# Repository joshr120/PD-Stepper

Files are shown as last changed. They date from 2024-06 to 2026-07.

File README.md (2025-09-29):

# **PD Stepper** - USB PD Closed Loop Stepper Driver & Controller
PD Stepper is a USB PD Powered Nema 17 stepper driver using the Silent Trinamic Driver TMC2209 controlled with a ESP32-S3 for IoT and other applications.

### Kits Available Now: [ThingsbyJosh.com](https://thingsbyjosh.com/products/pd-stepper) ###

<p float="left">
  
   
</p>

<p float="left">
   
  
</p>

Stepper motors are fantastic for projects, but assembling the necessary components—like a microcontroller, stepper driver, power supplies for both motor and microcontroller, and optionally an encoder can lead to bulkiness, high costs, complexity, and challenges in integrating them into compact or space-constrained designs. This project addresses these issues by consolidating everything onto a single board, eliminating the drawbacks with little to no compromises.

Full Video and build guide here: https://youtu.be/qECEGUZE04s?si=eJ1GiZOdusYehDCc

## Main Features: ##
- **TMC2209 Stepper Motor Driver:** Incorporates the TMC2209 stepper motor driver, renowned for its silent operation, high precision, and advanced features such as stealthChop™, spreadCycle™ and sensorless homing, ensuring smooth, silent and efficient motor control.
- **USB PD Power:** Utilizes the USB PD standard for power delivery, giving high power, a USB-C connector and no bulky 12 and 24V power bricks needed. It ensures compatibility with a variety of power sources and enabling seamless integration into existing setups. USB PD along with the TMC2209 can drive a stepper motor with upto ~50W of power.
- **Form Factor:** Super compact forma factor, designed to fit on the back of a common Nema 17 stepper motor
- **Onboard Rotary Position Sensor:** Integrates the AS5600 magnetic rotary position sensor for accurate and reliable absolute angle measurement, enabling precise positioning and closed loop control of the stepper motor.
- **ESP32-S3 Control:** The ESP32-S3 microcontroller serves as the brains of the system, providing ample processing power, built-in Wi-Fi and Bluetooth connectivity, and a rich ecosystem of development tools and libraries for easy customization and expansion such as **ESPHome** and **ESPNow**.
- Software or hardware selectable voltage: 5V, 9V, 12V, 15V or 20V all via USB PD
- Auxiliary connectors and buttons for flexablity and expansion
- Onboard 3.3V buck converter
- Motor temperature measurment

<p align="center">
  
</p>

## Kits Available For [Order](https://thingsbyjosh.com/products/pd-stepper) Now ##
   ### Subscribe on [YouTube](https://www.youtube.com/@ThingsbyJosh) for further updates. ###

<p align="center">
  
</p>

## Current Examples: ##
- Webserver allowing configuration, velocity and position control. (Comes pre-loaded on all kits, see [getting started](https://github.com/joshr120/PD-Stepper/tree/main/Getting%20Started) for how to use it.)
- Home automation with ESPHome and home assistant
- Wireless position copying from one encoder to another motor

## PCB: ##
PCB is a 4 layer 1.6mm custom PCB, this is what allows it to have its comapact form factor.
The Schematic, GERBERs and source files can be found in the PCB folder.

## Housing: ##
The Full Kits comes with an injection molded polycarbonate cover. This can also be 3D printed however PLA may not be suitable as the driver can get warm.

<p align="center">
  
</p>

## Cooling: ##
Stepper motor drivers can get warm under full load. The IC is cooled from the rear through a machined aluminium heatspreader which also acts as a spacer between the PCB and the motor. Two sizes of adhesive heatsinks can also stick to the top side with the larger one protruding through the housing and the smaller one siting just below the surface allowing the stepper to sit flat.

## Software: ##
The software is currently still evolving but current sample code should be more than enough to get you started

### ESPHome ###
The provided .yaml file allows you to control the motor through ESPHOME (setup as blinds in this example). It allows you to use the buttons as inputs and set the USB PD voltage. It also outputs the AS5600 encoder reading to be used within ESPHome. The USB PD voltage and stepper microsteps can be set at startup.

### Arduino Code ###
A few arduino examples are provided in this repo:
 - **Simple button control:**
   
      This example uses the buttons on the side to run the motor as at a variety of speeds as well as requesting a specified voltage from the PD controller. This can be used for a simple turntable and uses the simple step and direction interface to the driver

 - **Slider Webpage Control:**
   
      In this example the ESP32 hosts a webpage which allows you to wirelessly control the stepper motors speed with a slider. This utilises the [TMC2209 library](https://github.com/janelia-arduino/TMC2209) to configure the stepper driver.

- **ESP-NOW Sender and Receiver:**

     In this example one PD stepper board wirelessly sends its encoder value to another board which will mimic its position. This is an example of using ESP-NOW for low latency wireless communication.

  More info on the software can be found on the [software page](Software/README.md).

## Control ##
The primary way to control the PD Stepper is over WiFi (e.g ESPHome, ESP NOW or through a webserver) however there are many other ways you can control it

- Thanks to the pin mux on the ESP32-S3 the AUX connector (3 pin JST SH) can be used to send/receive commands over many different protocols. For example: Serial UART, I2C and standard STEP & DIR signals.
- By Using the I2C connector as well as the AUX connector you could daisy chain many PD Stepper boards together.
- The standard Qwiic / Stemma QT I2C connector (4 pin JST SH) means you can connect a wide range of sensors which could be used for control (for example a [Rotary Encoder](https://www.adafruit.com/product/5880) or a [Light Sensor](https://www.adafruit.com/product/4162))

- The 3 buttons on the side of the board can be set to control speed and/or position

- Serial commands can be sent/received through the USB-C connector (Note if your device sending the commands cannot provide enough power you may need an injector of some kind)

- The ESP32-S3 also has built in BLE (Bluetooth Low Energy) which could be used for control.

- End stops can also be connected to the AUX Connector (3 pin JST SH)

## Setting the driver voltage ##
The USB PD voltage can be set by toggling 3 GPIO pins on the ESP32. This can be configured on the fly to change voltage.

By default the board will ask for 20V at startup if the microcontroller does not set the config pins fast enough. If for whatever reason your motor cannot handle 20V you may want to set resistor R18 to a set value or ensure the pins are set on startup. The voltage can be configed by software on the fly as required. 

When programming the board it is likely your computer will only be able to provide 5V, the "Power Good" line from the PD controller can tell the ESP32 it is not receiving the voltage it is asking for and in this case you should proably not enable the stepper driver (as done in the example code)

NOTE: You must use a USB PD power brick/power bank which can provide the required voltage and current along with a suitable USB-C cable. QC (Quick Charge) is not currently supported.

## Setting the driver Current ##
The motor current can be set either in hardware with the onboard potentiometer or over the TMC2209 serial interface (see the [TMC2209 library](https://github.com/janelia-arduino/TMC2209) for more info on serial comms)

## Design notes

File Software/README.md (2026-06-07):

# **PD Stepper** - More Software Info

#### If you just received your PD Stepper see the [Setup Instructions](https://github.com/joshr120/PD-Stepper/tree/main/Getting%20Started) for how to get started

## Arduino Upload settings: ##
When uploading software with the Arduino IDE ensure you have first installed the ESP32 Add-on in Arduino IDE there are [many tutorials](https://randomnerdtutorials.com/installing-esp32-arduino-ide-2-0/) on how to do this.

The Board type should be set as "ESP32S3 Dev Module"

USB CDC on Boot should be set to "Enabled"

upload settings

## ESPHome: ##
>If you have not used ESPHome before follow the offical [getting started guide](https://esphome.io/guides/getting_started_hassio.html). Select ESP32-S3 as the board type. The custom .yaml can then be copied from the repo into the configuration editor. Ensure you also add you WiFi SSID and password to your "Secrets".

The **PD-Stepper-Blinds-Advanced.yaml** config file uses the [custom TMC2209](https://github.com/slimcdk/esphome-custom-components/tree/master/esphome/components/tmc2209) component by [slimcdk](https://github.com/slimcdk). It also uses the AS5600 encoder so that if the blinds are manually moved it will not lose its end positions. Thanks to the custom componenet the example cuses stall gaurd for sensorless homing. PD voltage and other settings can easily be configured in the settings section at the top of the code. 
> This will use the power on position as the OPEN position.

> If the motor spins but the cover stays in the "open" position it means either your encoder is not working or your motor is spinning in the opposite direction releative to your encoder. You can swap which lambda function is commented out to reverse the encoder direction. 

> Sensorless homing (Stallguard) is enabled whoch means if the motor stalls this becomes the new home (OPEN) position, you may need to tune the threshold and current values to get this to work well. See the settings section at the top to tune/disable.

The **PD-Stepper-Blinds-Simple.yaml** config file simply treats the TMC2209 as a a4988 driver. The microsteps and PD voltage are set at startup by GPIO pins and the motor is driven via the STEP and DIR pins.

The **PD-Stepper-Position-Control.yaml** config also uses the [custom TMC2209](https://github.com/slimcdk/esphome-custom-components/tree/master/esphome/components/tmc2209) component by @slimcdk. It is a more stripped down version of PD-Stepper-Blinds-Advanced.yaml allowing you to set the position of the motor using a simple slider. A good base for use cases other than blinds.

These examples also present the buttons, LEDs, power good and bus voltages to the ESPHome interface so you can do what you like with them.

## Flashing a precompiled binary online: ##

There is a great online tool called [ESPConnect](https://thelastoutpostworkshop.github.io/microcontroller_devkit/espconnect/) which can be used to flash the board without downloading any software. 

The following steps will show you how to flash the default webserver example.

**1.** Plug the PD Stepper into a PC, Open [ESPConnect](https://thelastoutpostworkshop.github.io/microcontroller_devkit/espconnect/) and press Connect.
image (3)

<br>
<br>

**2.** Select your board, COM number will be different but naming will be similar.
image (4)

<br>
<br>

**3.** Go to the "Flash Tools" page and select the `PD_Stepper_Web_Server.bin` file (Download from [here](https://github.com/joshr120/PD-Stepper/tree/main/Software/PD_Stepper_Web_Server)).
image (5)

<br>
<br>

**4.** Press flash and confirm
image (6)

<br>

Feel free to reach out at [info@thingsbyjosh.com](info@thingsbyjosh.com) if you have any problems.

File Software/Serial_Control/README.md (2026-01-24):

# PD Stepper: Serial Control Guide

Upload the Serial_Control.ino script to control your PD Stepper over serial.

## Connection Options

The controller supports dual-input serial communication. You can send commands through either interface; the controller will process the command and respond back on the same port it was received.

### 1. USB Connection (`Serial`)
* **Physical Port:** Standard USB-C connector on the ESP32-S3.
* **Baud Rate:** 115200

### 2. AUX Connector (`Serial1`)
* **Physical Port:** AUX connector (3 pin JST SH connector).
* **Pins:**
    * **Pin 1 (GND):** Ground pin.
    * **Pin 2 (AUX1 - TX):** Transmits data from the ESP32.
    * **Pin 3 (AUX2 - RX):** Receives data into the ESP32.
* **Baud Rate:** 115200

---

## Control Modes & Switching

The controller operates in a "last command wins" state machine. It switches between modes automatically based on the command received:

* **Position Mode:** Triggered by the `deg=` command. The motor will calculate the distance to the target angle and move using the speed defined by `speed=`.
* **Velocity Mode:** Triggered by the `vel=` command. This immediately overrides any active position targets and causes the motor to spin continuously at the requested rate.

> **Note:** Sending `vel=0` will stop the motor but keep it in Velocity Mode. To return to a specific angle, you must send a new `deg=` command.

---

## Encoder Integration (`MOVE_FROM_ENC`)

When `closed_loop_type` is set to `MOVE_FROM_ENC`, the controller uses the AS5600 Magnetic Encoder to verify its physical orientation before moving.

1.  **Read:** It captures the current mechanical angle from the encoder.
2.  **Calculate:** It determines the error (delta) between the current encoder position and your `deg=` setpoint.
3.  **Correct:** It generates the exact number of microsteps required to bridge that gap.

This allows the system to remain accurate even if the motor was moved by hand while the driver was disabled.

---

## Full Command List

| Command | Data Type | Description |
| :--- | :--- | :--- |
| `deg=` | Float | **Switch to Position Mode:** Move to absolute angle. |
| `deg_rel=` | Float | **Switch to Position Mode:** Relative move to absolute angle. (add or subtracts from current setpoint) |
| `speed=` | Float | Set travel speed for `deg=` movements (deg/s). |
| `vel=` | Float | **Switch to Velocity Mode:** Spin at fixed rate (deg/s). |
| `steps_per_rev=` | Int | Set motor physical steps (200 or 400). |
| `enable=` | Bool/Str | Enable/Disable driver (`1`/`0`, `TRUE`/`FALSE`, `enabled`/`disabled`). |
| `microsteps=` | Int | 1, 4, 8, 16, 32, 64, 128, or 256. |
| `voltage=` | Int | USB PD Request (5, 9, 12, 15, or 20). |
| `current=` | Int | Set run current as a percentage (0-100). |
| `standstill_mode=`| String | `NORMAL`, `FREEWHEELING`, `BRAKING`, or `STRONG_BRAKING`. |
| `closed_loop_type=`| String | `OPEN_LOOP` or `MOVE_FROM_ENC`. |
| `mappingDirection=`| Int | Reverse motor logic relative to encoder (`0` or `1`). |
| `verboseOutput=` | Int | Toggle confirmation messages (`0` or `1`). |
| `get_angle` | N/A | Returns current total encoder angle in degrees. |
| `values` | N/A | Lists all current configuration settings. |
| `led_flash` | N/A | Flashes LED1 twice for identification. |
| `help` | N/A | Displays summary of commands. |

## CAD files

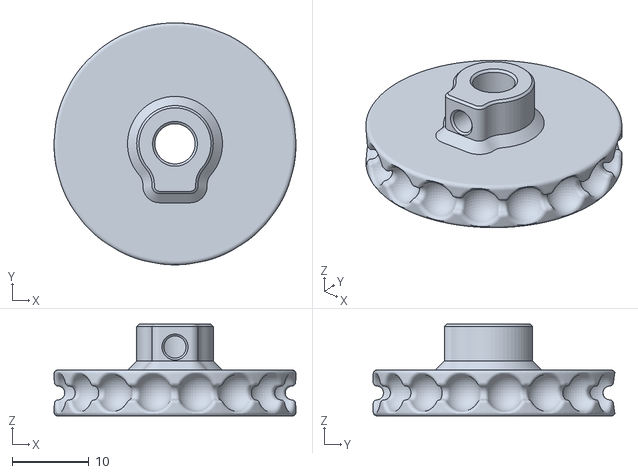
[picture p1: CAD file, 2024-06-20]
Hardware/Accessories/Blinds Wheel.stl
31.6 x 31.6 x 12.0

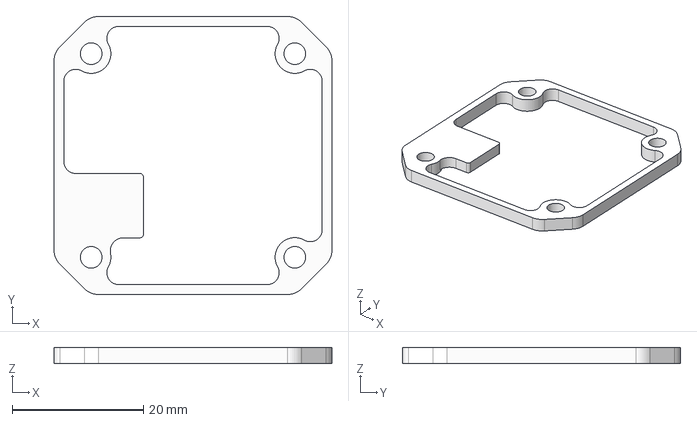
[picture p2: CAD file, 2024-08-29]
Hardware/Heat Spreader (2.5mm).step
42.3 x 42.3 x 2.50 mm

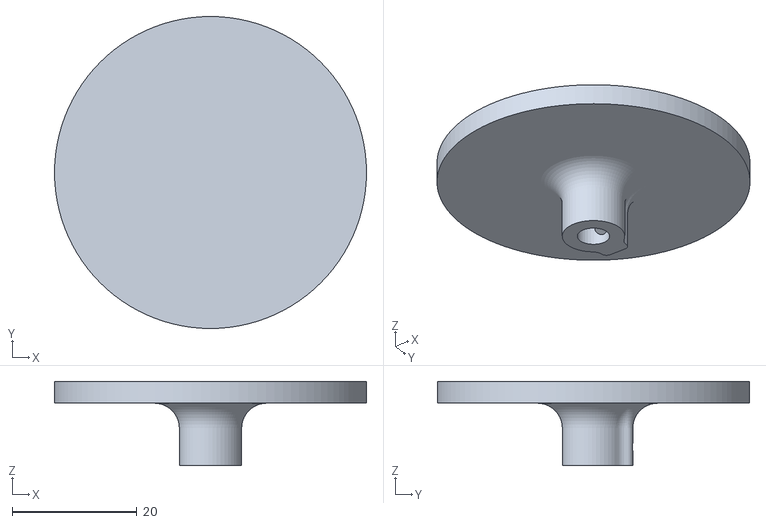
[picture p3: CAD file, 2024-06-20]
Hardware/Accessories/Turn Table.stl
50.0 x 50.0 x 13.5

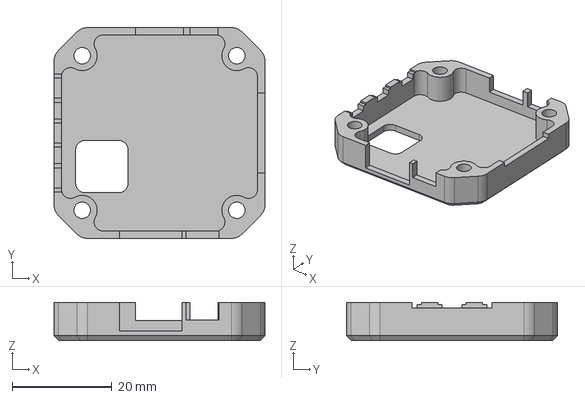
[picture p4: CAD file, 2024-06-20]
Hardware/Machined Housing.step
42.3 x 42.3 x 7.70 mm

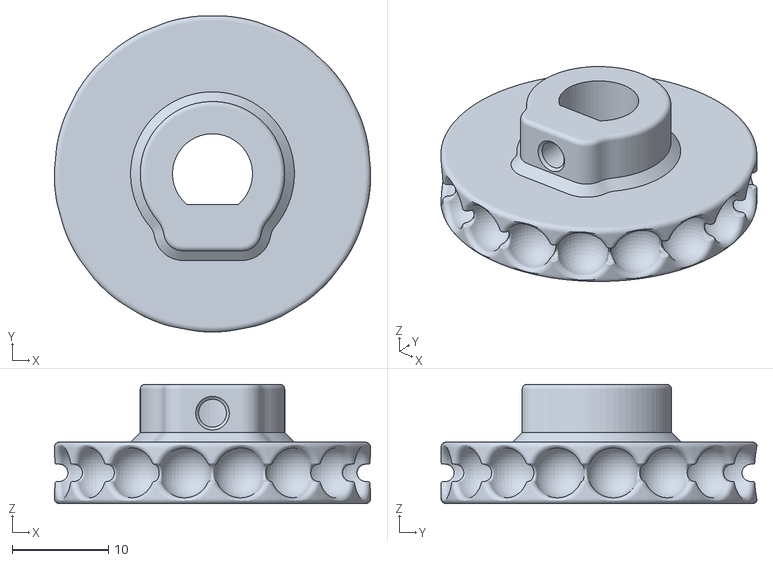
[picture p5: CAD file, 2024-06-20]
Hardware/Accessories/Wheel (8mm Bore).stl
32.8 x 32.8 x 12.4

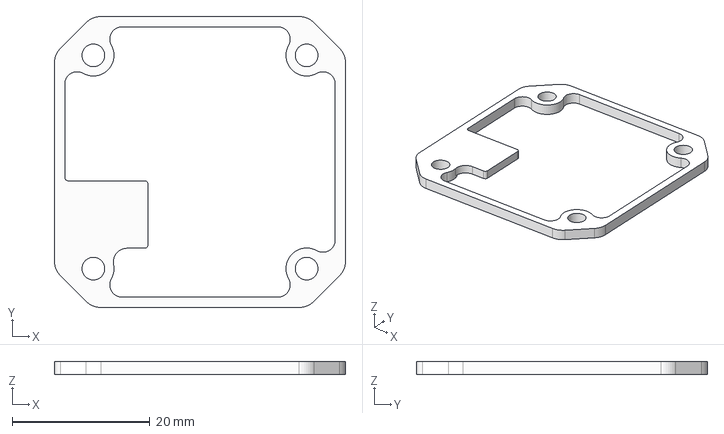
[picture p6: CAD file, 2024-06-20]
Hardware/Heat Spreader.step
42.3 x 42.3 x 1.95 mm

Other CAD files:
Hardware/Cover.stl

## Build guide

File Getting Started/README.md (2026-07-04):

# **PD Stepper** - Getting Started
If you just received your PD Stepper this will show you how to spin a motor and configure the driver using the firmware pre-installed on the board.

(Click [here](http://thingsbyjosh.com/canbus-stepper-getting-started) for the CANBUS Stepper getting started guide.)

⚠️ **Warning:** Stepper motors should never be back driven at a high speed as they can act as a generator and cause damage. This is especially important if your PD stepper board is connected directly to a computers USB port

## Assembling a kit onto a Nema 17 ##

Assembly is also shown in [this video](https://www.youtube.com/shorts/9y9dA18rnVY).

For easiest assembly your motor should have the stardard 6 pin JST PH connector, and the included screws (M3x40mm) are best suited for a 34mm length motor.
For example the Hanpose 17HS3401S, available on [Amazon](https://www.amazon.com/Captive-Stepper-17HS3401S-4-Lead-Printer/dp/B0G9KRJFTY) and [Aliexpress](https://www.aliexpress.com/item/1005006577156384.html).

### 1. Install the magnet onto your motor (only needed for reading encoder position)
   
   Carefully superglue the included diametrically magnitised magnet onto the centre of the motor shaft.  

   Only a very small amount of glue is required, take care not to get any in the motor bearing.  
   
   
   
### 2. Remove the original motor screws




### 3. Peel off the protective film and add one of the included heat pads onto the heat spreader

  Ensure this is added on the recessed side of the heat spreader
  



### 4. Place the spacer onto the motor ensuring it is in the orientation show

Note. If you are not using the heatspreader/spacer (partial kit) ensure the board is not resting directly on the motor as this could short out the traces on the underside of the PCB. Use washers or an insualting layer.



### 5. Add the PCB

Again ensure the PCB is installed in the orientation shown so the motor connectors as well as the heat pad line up




Note: Some motors may have longer shafts that make the magnet sit higher. If the sensor contacts the magnet, add spacers to raise the PCB.

### 5. Add the cover and new countersunk screws

   The included screws are best suited for a 34mm length Nema 17 you may need longer or shorter ones depending on your motor. (included ones are M3x40mm)
   
   
   

### 6. Add the heatsink

   Use the larger heatsink if you plan on running the motor for long periods and/or at high currents
   
   
   

### 7. Plug in motor loom

 There are 2 looms provided in the kit for different motors, try one and if at the next step your motor stutters/doesnt spin, power off the board and try the other one. 

  Note. Do not disconnect/connect the motor while the board is powered.

  

<br>
<br>

## Running the Webserver ##
**1.** Connect the PD Stepper to your PD power supply using a USB C to C cable (Needs to be Type C as USB PD does not support Type A).

**2.** Open a phone/computer and connect to the WiFi network named "PD Stepper"

**3.** Open a browser and type in the IP Address **192.168.4.1**


   
**5.** From here you can use velocity/postion control and play around with different settings.

**6.** The current is set as a percentage of the maximum possible current (1.92A). You will want to set this to match the current rating of your motor (or lower to stay cooler) E.g for a 1.8A motor set to 90% as 90% * 1.92A = 1.73A

Note: When using the webserver example the value is set here and the potentiometer is ignored. When using the advanced ESPHome examples this can be set with by changing the `run_current` value.

**7.** For your own projects this code as well as others (such as ESPHome config) can be found [HERE](/Software)

**8.** The buttons on the side can also be used to change the velocity

## Trouble Shooting ##
- The motor will not spin unless the board is receiving correct the voltage requested from the PD Source. So ensure your brick can supply the correct voltage and supports USB PD. The requested voltage can be adjusted on the fly in the webserver.
- If the "PG Status" is showing "Power Bad" ensure you are using a USB PD power supply (greater than 45W preffered) and that you are using a Type C to C cable.
- If the motor is not spinning smoothly, power off the board and try the other motor cable provided in the kit.
- If no WiFi network is created and LED 1 (blue) does not blink at startup, the correct software may not be installed. There are two ways to load the latest web server example software:

    The simplest method is to flash the precompiled binary using an online tool. See the instructions at the bottom of [this page](https://github.com/joshr120/PD-Stepper/tree/main/Software)

    Alternatively, you can compile and flash the Arduino source code located [here](https://github.com/joshr120/PD-Stepper/tree/main/Software/PD_Stepper_Web_Server)

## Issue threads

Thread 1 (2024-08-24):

Great idea, what are the memory limitations?

FlailAway, 2024-08-24:
The ESP32 appears to be limited to around 160KB. After setting up for local wifi, how does one handle data storage?

Streaming data-feed over wifi to a 3D-printer etc., would be a risky effort I would think, so a few GB of memory would be handy to store data in one complete block for it to feed forward.

Driving the blinds is a nice thing, but with closed-loop (terrific addition) greater things would need greater storage memory. No?

I don't do "G" or "YT" to comment there. :)

joshr120, 2024-08-24:
Instead of storing all of the movements on the devices you would feed them into a buffer (over USB or WiFi etc). Many people have used ESP32's to run CNC machines using this exact premise (See fluid NC for example). And the common GRBL software runs on an Arduino Uno which has significantly less memory, so I do not think this is an issue if you implement it correctly

Closed 2024-09-13.

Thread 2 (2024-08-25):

BOM - Bill Of Material

glennswest, 2024-08-25:
Great design.
BOM?

joshr120, 2024-09-18:
Send me an email at info@thingsbyjosh.com and I can get you a copy of the BOM

Closed 2024-09-18.

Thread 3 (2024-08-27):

GREAT IDEA! But more to add to it!!!!!

Cyrille-de-Brebisson, 2024-08-27:
Hello,

I LOVE YOUR IDEA. I just ordered one of the "standard" closed loop controler for a nema17, but yours is definitely one step above...

However, I have some requests/additional ideas here...

I am an amateur astronomer, and I make telescopes.
Telescope typically need 3 to 4 motors to work. 2 for moving the telescope, 1 for moving the focus and one for the filter wheel.
One issue that we have ALL THE TIME is cable managements. A typical astrophotography setup is a cable mess!

So, here is the request, Could the Aux connector be reworked so that it has:
- Data AND power
- They are 2 of them, one in, one out, in order to allow to daisy chain motors?

Thanks,
Cyrille

joshr120, 2024-08-27:
Hi Cyrille,

Thanks for the ideas, those particular connectors being used for AUX are only rated to 1 amp so would not have enough power to daisy chain multiple motors together. If you had multiple motors all running at full power powered off one USB PD port you could reach the max power draw pretty fast.
However, if you really wanted to daisy chain them there are solder pads on the underside where you can access/inject the PD voltage directly (just make sure you don't use the USB connector at the same time). Using I2C you could then daisy chain the data with the existing AUX and qwiic connectors . You could also use something like ESPNOW if you wanted to do this wirelessly.

Cyrille-de-Brebisson, 2024-08-27:
Hello,

I understand...

- Is it possible to have nice easy to solder vias for power daisy chain, with 2 of each (2 gnd, 2 power)? to make it easy and stable? something like a 2*2 1/10" header type thing?

- I see that you have a number of LED on the system. Some seems to be programmable (great), but others seems to be always on type thing. It is possible to have them controlable so that they can be turned off? As you can imagine, LEDs are not what you want near a telescope :-)

Cyrille

joshr120, 2024-09-18:
There is not currently room for extra power headers on the board at the moment, the solder pads on the underside are the best I could fit to stay within the NEMA17 form factor.

The additional LEDs are not currently set up to be able to be turned off in this version, although they are derated to not be full brightness. They can also be removed (or covered) if they are not needed.

fladdie, 2024-09-26:
Can bus would be a great feature

001oc, 2024-10-10:
Kicad: https://github.com/user-attachments/files/17332545/PD-Stepper.zip

EasyEDA: https://oshwlab.com/adamscamden2/pd-stepper

dwmw2, 2025-02-10:
What about expanding the motor connector to 6 pins to allow for power and ground through that?  I've just been playing with feeding power from behind, using S1761-R42 terminals. It works, but it's a real pain to solder up and assemble by hand, even in a mount 3D-printed for the purpose.

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

Using Veroboard is just as painful to solder but at least gives a better mechanical connection.

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

I'm tempted to get some tiny board professionally manufactured. Wonder if they'd be useful to include as an option in the kits? It could even be done as a full sized 42.3x42.3 board with the spring contacts on top and the PH connector on the bottom, designed to sit under the metal spacer/heatsink if the full kit?

joshr120, 2025-02-10:
Expanding the motor connector to 6 pins would mean that the motor loom could be plugged in the wrong way around (as the Nema 17 also has a 6 pin PH). This would also require the molds to be modified for the injection molded covers.

I do quite like the pogo pin idea.  The only problem I see with having the connector underneath like you do is it affecting the spacing between the magnet and encoder.  I guess you could add a spacer underneath the magnet or stack another magnet on top.
However a custom board could possibly replace the aluminum spacer and bring the connector out to the side and would not affect the form factor too much as you would already have wires coming out.

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

This mock up has it in front of the USB connector which would be a pain for programing but you really don't want both plugged in at the same time and this could fry your computer. This uses a 1mm board + a 1.6mm board to get the spacing as well as allowing a recess for the pogo's to sit in. Let me know what you think.

Could also be nice to use something which can carry a bit more current than a PH connector so that daisy chaining power could be an option.

dwmw2, 2025-02-10:
If I wanted it that side I'd just use the USB connector. I'm trying to keep the wires all on one side. This is the prototype version (inward facing, as I'm not allowed to dig holes in the wall until the proof of concept is working).

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

I'm trying to avoid that extra cable at the top. (Those green LEDs are too bright too but I'll try to hide those with a black cover).

I have my magnet mounted inside the gear, protruding through the piece of the mount that the power connectors are in, so that part works OK here. And I've found that soldering the spring connectors to a Dupont header designed for board-mounting seems to work...

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

joshr120, 2025-02-11:
Ah I see, did not realize your goal was to keep everything on one side. I thought you just wanted a way to power it with straight DC rather than USB PD.  Either way a custom PCB or 2 would probably be the way to go.

dwmw2, 2025-02-11:
The spacers require about 3mm between their base and the underside of the PD stepper board, so I think I'm happiest with my setup of soldering them to a Dupont header inset into the mount, rather than the thickness of an extra PCB.

But since someone else had already asked, I figured it was worth mentioning the possibility of a second PCB to supply power.

FWIW I also just realised I *do* need a plug at the top for the AUX pin which will be connected to the reed switch at the top of the blind, for homing. I'll probably bring that single wire straight down into the same plastic piece and bring it to a 3-pin header with the Gnd and Vbus I already have there. Are there unused GPIO pins on the ESP32? Maybe the QWIIC connector could have its *own* pins for its own i2c bus (or other purposes). The i2c bus with the as5600 encoder is going to be permanently busy with polling anyway, isn't it? Not much bandwidth for anything else.

joshr120, 2025-02-11:
Currently the QWIIC connector is on the same I2C bus as the as5600 as I was getting low on pins and that is how most of the QWIIC ecosystem works. If the encoder is being polled very fast it may use a fair bit of bandwidth but would also use a far bit of CPU bandwidth at the same time while reading, so a second bus may not be of too much use other than if there are address conflicts or you are getting fancy with multitasking.

I may look into putting it onto its own bus in a future version, but for something like a limit switch this is exactly why the AUX connector is there.

dwmw2, 2025-02-11:
The encoder needs to be polled fast, or it misses revolutions. I've been playing with it, and ESPHome going out to lunch seems to be the reason why my tracking was wrong. I occasionally see warnings like

```
[09:19:26][W][component:237]: Component as5600.sensor took a long time for an operation (4184 ms).
[09:19:26][W][component:238]: Components should block for at most 30 ms.
```
So the blind closes correctly because it did calculate the correct number of steps to turn the motor, but the encoder tracking only thinks it's closed part way. So when it's told to open again, it only goes part way.

But then #22 happened while I was experimenting and now I don't have a laptop so it'll be a little while before I can experiment some more...

joshr120, 2025-02-11:
yes you need to be reading fast enough to catch a wrap around. Just did some quick timing with Arduino and a read takes ~500 microseconds so you would need to be polling around 2000Hz to max out the bus.  The max speed of a stepper is _relatively_ slow so you should never run into the problem of not being able to poll fast enough to catch a wrap around.
It does sound like your problem is ESPHome related. It may actually be polling too fast and hogging the CPU which ESPHome may not like, you could try slowing down the polling rate.

dwmw2, 2025-02-11:
I think I'd already backed the poll rate down to 50ms from the originally configured zero, after seeing ESPHome watchdog resets because the idle task was never getting to run. That should have been fine.

Closed 2025-05-28.

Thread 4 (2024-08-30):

KICAD files available

001oc, 2024-08-30:
great idea you realized, matching a project I was looking a solution for some time now. I would like to expand the projekt abit for my needs are KICAD files (or something else) available?

Thanks

Johnr24, 2024-09-10:
Yes, +1 Please supply the kicad or original source files. You can't truly call your project open-source if you aren't providing the easiest and least resistive way of allowing users to make changes and alterations...

joshr120, 2024-09-18:
The PCB Source files are not available at this stage sorry, feel free to use the schematic and GERBERs to base your project on.

Johnr24, 2024-09-18:
this is not compliant with GPL see section 7. Gerbers and Schematics are effectively compiled binaries and not source files,

001oc, 2024-09-18:
I think it would and should be his decision the way he feels it would be open source or something similar ... and we have to accept it instead of poking arround. I think it is well made and I dont blame someone to try to make some money to get back its efforts making some valuable pcb. And its way not to complicate to rebuild it - what I am doing right now. I am doing currently a rough "rebuild" of the pcb. Its purpose should be to help that people which want do expand or modify the good base idea - as me. I think that this is not disturbing the business of @Johnr24 as the onces that want to modify the pcb even are no potential customer of @Johnr24 - I think that could be a point of view even for @Johnr24 - but as I sayed, not my decision.

I am happy for the material that is already posted and it helps me to redesign the pcb quit quickly I think - from my point of view this is more than enough and I am thankful for that.

SoupySoups, 2024-10-10:
I know im gonna get some backlash for easy eda but i have recreated the board with my own differences [here ](https://oshwlab.com/adamscamden2/pd-stepper). Everything works great from my tests.

001oc, 2024-10-10:
Thanks alot to @SoupySoups .

I have imported your stuff to Kicad roughly.

From my quick overview it seems to be working - at least it is a proper base to work further.

[PD-Stepper.zip](https://github.com/user-attachments/files/17332545/PD-Stepper.zip)

Johnr24, 2024-10-10:
Excellent. Amazing work!  Could I suggest starting a fork of this project
that is truly and correctly open source?

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

tmarkson, 2024-10-10:
The fact that you could redraw Josh's design from the files that he provided suggests the project is open enough already!

joshr120, 2024-10-11:
Now that pre-orders are starting to be shipped I have published the PCB Files (Altium format).
I also had a quick look at @SoupySoups easyeda project and can offer a few pointers which will help it work better if someone plans on using those files.

Main reason I did not release them earlier was to stop someone simply slapping their logo on it and beating me to market while I was ramping up production & waiting for molds to be made. (Full kits will now come with injection molded polycarbonate covers and a black anodized heat spreader/spacer).

SoupySoups, 2024-10-11:
> Now that pre-orders are starting to be shipped I have published the PCB Files (Altium format). I also had a quick look at @SoupySoups easyeda project and can offer a few pointers which will help it work better if someone plans on using those files.
>
> Main reason I did not release them earlier was to stop someone simply slapping their logo on it and beating me to market while I was ramping up production & waiting for molds to be made. (Full kits will now come with injection molded polycarbonate covers and a black anodized heat spreader/spacer).

I understand your reasoning, I recreated the design not to sell the product but to put in a project i am currently designing in which i needed multiple of these steppers. I understand the extra value that you provide other than the raw pcb but i did not need the extra parts and the cost for 8x kits per unit of my design just did not make economic sense for my application.

The copy in easyEDA was rushed and im not that great at PCB design but all functionalities (i removed some of your features that I didn't need to further save costs and make layout easier, aka. buttons and expansion). Everything seems to work well though.

In all, yeah, your board is reeeeeally nice. I wish i had your skills, and I agree, mine is not meant to be sold in a kit, its rough.

> The fact that you could redraw Josh's design from the files that he provided suggests the project is open enough already!

In response to this, its tough, wouldn't call having to go through grbl files manually "open".

Josh I appreciate this and am thankful for what was shared, even if difficult. I notice you dont have any example code with measuring vbus voltage, using the temperature sensor, or using the AS5600 in combination with the TMC2209 for closed loop stepper control. If you would like, I would be more than happy to share my code, implementing such features.

Closed 2024-09-18.

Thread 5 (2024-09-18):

not compliant with GPL

Johnr24, 2024-09-18:
as the source kicad files have not been provided,
this is not compliant with GPL see section 7. Gerbers and Schematics are effectively compiled binaries and not source files,

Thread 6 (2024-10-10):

Kicad and EasyEDA files available now...

001oc, 2024-10-10:
For further development there are files for Kicad and EasyEDA available:

Kicad: https://github.com/user-attachments/files/17332545/PD-Stepper.zip

EasyEDA: https://oshwlab.com/adamscamden2/pd-stepper

Cyrille-de-Brebisson, 2024-10-11:
Hello,

One request, if possible. Would it be possible to add 2, 2 pins headers with GND and vbus?

The aim would be to be able to bring power to stepper "one" (either using USB or a 12V power supply), and then daisy chain 3 or 4 steppers from there. I do not have a huge power consumption (around 1A for the 2 main motors, who are only running for short intervals), and around 0.5A for the 2 others which will run around 1 minute per night each...

I tried looking at the PCB to see if I could do it myself, but I am way not good enough to start playing with such a non-trivial PCB (is it a 4 layers PCB?)

Thanks,
Cyrille

001oc, 2024-10-11:
> Would it be possible to add 2, 2 pins headers with GND and vbus?
I think there seams to be enough free space to do so. Anyway, I wouldn't do that this way,

>  (is it a 4 layers PCB?)
no, its a "simple" 2-layer pcb

Cyrille-de-Brebisson, 2024-10-11:
Hello,

>>   Would it be possible to add 2, 2 pins headers with GND and vbus?
>I think there seams to be enough free space to do so. Anyway, I wouldn't do that this way,
How would you do it?

I am trying to use these motors to make a telescope mount...
Telescopes have WAY to many cables! this should give you an idea of the mess that you can get into :-) https://i.ytimg.com/vi/Ip0Ok9OncNY/maxresdefault.jpg

Anyhow, on the other hand, we DO have 12V available to us as all astro equipement uses "raw" 12V...
Typically, we use a slow discharge car battery with a 12V boost converter to generate said 12V...

However, finding a USB-C power supply (portable) that will have 4 PD output and will run on 12V would be quite hard...
Plus it will cause tnagled wires as the scope moves..

Hence the idea of being able to connect the motor in a daisy chain (or distribution tree as needed) in order to reduce cables and cable snags.

Cyrille

joshr120, 2024-10-11:
Now that pre-orders are starting to be shipped The Altium Source Files been added to the repo.

Closed 2024-10-11.

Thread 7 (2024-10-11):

proposed Altium sources and existing Kicad and EasyEDA sources

001oc, 2024-10-11:
Now that pre-orders are starting to be shipped The Altium Source Files been added to the repo.

_Originally posted by @joshr120 in https://github.com/joshr120/PD-Stepper/issues/6#issuecomment-2406915418_

I can't see the altium files as of now and there is even no specific hint where to look specifically. Even most people will not have a Altium license. For that reason I will repost the Kicad and easyEDA sources to get people an easy way to work further on this project.

As @joshr120 stated the reason for not revealing the sources till now is not to be beaten in getting his project to market. That should be no problem now. For that reason it  shouldn't be neccessary to close the issue that fast because that will prevent others to get the information where to get sources - otherwise one could have the impression @joshr120 intention is to supress such information for an gpl-project.

Please let this issue open for now.

Kicad: https://github.com/user-attachments/files/17332545/PD-Stepper.zip

EasyEDA: https://oshwlab.com/adamscamden2/pd-stepper

joshr120, 2024-10-11:
I committed the files but forgot to press push 🤦 my bad. The files can be found in the PCB folder. They are in Altium format as that is what the board was designed in. These can however be [converted to your PCB design software of choice.](https://refcircuit.com/articles/18-how-to-import-altium-designer-pcb-board-in-kicad.html) From my quick look at the easyeda design by @SoupySoups there were a couple of potential issue I spotted as well as not all features supported so I would recommend any future modifications are based off the fully tested files now that they are available.

I closed the previous issue as the original fully tested PCB files are now available so I considered it solved. Can keep this issue open for a while if you would like? The closed issues are still available for anyone to see.

001oc, 2024-10-11:
Thanks alot :-)

SoupySoups, 2024-10-11:
> I committed the files but forgot to press push 🤦 my bad. The files can be found in the PCB folder. They are in Altium format as that is what the board was designed in. These can however be [converted to your PCB design software of choice.](https://refcircuit.com/articles/18-how-to-import-altium-designer-pcb-board-in-kicad.html) From my quick look at the easyeda design by @SoupySoups there were a couple of potential issue I spotted as well as not all features supported so I would recommend any future modifications are based off the fully tested files now that they are available.
>
> I closed the previous issue as the original fully tested PCB files are now available so I considered it solved. Can keep this issue open for a while if you would like? The closed issues are still available for anyone to see.

Would you be willing to share such issues? From initial testing, all features that I chose to implement seem to be functioning correctly.

joshr120, 2024-10-12:
Sure, I have not looked too in depth but here are couple of things I noticed that may affect performance. Other than the features you intentionally did not include the first thing I noticed was the setup of the current sensing resistors for the TMC2209. These carry the full motor current and currently your design does not have well defined return path from the resistors back to the IC. The GND pad on the TMC is not accessible on the top layer and the layers are only really stitched with the vias in the corner mounting holes. Adding a few GND vias near the GND pads of these resistors would help greatly.

Here is a screenshot from the TMC2209 datasheet which explains why it needs to be carefully considered:
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

I would also probably want to increase the trace width between the current sense resistors and the TMC as these take the full motor current.

Decoupling caps for the various IC's as well as the VIN and VOUT caps for the 3.3V reg should be placed as close to the relevant pins as possible.

Hope these tips help with your future designs!

SoupySoups, 2024-10-12:
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

Oh yeah, that gnd section isnt very connected 😅

Closed 2024-10-11.

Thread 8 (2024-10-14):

Not a problem, but a question

Cyrille-de-Brebisson, 2024-10-14:
Hello,

I have noticed with the traditional drivers that microsteps are NOT all equal.

For example at 1/8th using an A4988, the various microsteps are definitely not 0.225° appart (360/200*8). Although 8 microsteps do indeed equal 1.8°
DRV8825 at 1/32 are much better, but even then, microsteps are not concistent...
(These are tests that I did using a mirror on a motor and measuring the displacement of a laser 5m away)...

So, here is the question. In your design you have a TMC2209 with 256th microsteps, but also the 14 bit position sensor (which give the equivalent of a 1/80th microstep precision, and is, itself not truly linear according to the datasheet)...
Would it be possible to generate a 51200 entry table that gives, for each of 200*256 microstep, the sensor reading in order to characterize the real position for each microstep?

Thanks,
Cyrille

joshr120, 2024-10-15:
Hi Cyrille,

The "microstepping consistency" of the TMC2209 should be a lot more accurate than the A4988.

To answer your question I imagine the characterization you are looking for would likely change depending on a number of factors such as static friction of the motor, winding quality, how centered the magnet is on the encoder, etc. The linearity of the AS5600 will also depend quite a lot on how centered the magnet is on the sensor (Although this would stay consistent for each setup so could be calibrated out)

However, I have done a quick test as you asked and made a table showing encoder reading vs microsteps. (400*256 = 102400 data points as my motor was a 400 step per revolution stepper). Note this test was just run at 5V with not a whole lot of effort put into exactly centering/spacing the magnet.

Data can be found here: https://docs.google.com/spreadsheets/d/1EG3RP1kZXmzleNbZcZI58o96MoQLjMxshMYBuX7mUSY/edit?usp=sharing

This data also does not answer the first part of your comment as the encoder is 14 bit (0.088 deg accuracy) and each microstep in this case is only 0.0035 degrees

Thanks,
Josh

Cyrille-de-Brebisson, 2024-10-15:
Woha, thanks!

I will be looking at the data and commenting back here, but thank you so much for doing the work!

Cyrille

joshr120, 2024-10-16:
The difference between your "Series 1" and "Series 2" was just because of my hastily written test code which had a routing error accumulating for each step taken. The "Series 2" in your graph is the correct error measurement. I have fixed the code for these next tests.

The longer oscillation is the most likely due to the sensor not being aligned with the magnet very well. Because this stays consistent for each setup (and returns to 0 after each rotation) it can be easily calibrated out by running the motor with no load and recording the expected position vs encoder reading.

I have re-run the test with a simple calibration for comparison. The calibration was very simple and just a lookup table of encoder reading vs "actual" position.

The data has been added to a new tab in the [spreadsheet](https://docs.google.com/spreadsheets/d/1EG3RP1kZXmzleNbZcZI58o96MoQLjMxshMYBuX7mUSY/edit?usp=sharing).

And here is the a graph showing error with and without calibration.
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

I am not aware of any higher resolution drop in replacements for the AS5600 as most higher resolution encoders use a SPI or alternative interface to also get additional bandwidth.

Cyrille-de-Brebisson, 2024-10-16:
Hello,

1.2° of error seems A LOT!

But who cares, once it is calibrated, it indeed drops to what amounts to 0! Great job...

Thanks for taking the measurements..
Cyrille

Closed 2025-05-28.

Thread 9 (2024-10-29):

Beautiful cover! Where did you get injection molded polycarbonate cover

wasauce, 2024-10-29:
@joshr120 - wonderful project here and really compelling.

I am working on a cover for a totally different project (no stepper motor) and I am inspired by your injection molded polycarbonate cover. Could you share more about where you get these covers made? I am new to this and looking to learn.

I don't have a good sense of the cost as compared to some 3d printed solutions and I'd love a pointer in the right direction.

Thank you!

Closed 2024-11-17.

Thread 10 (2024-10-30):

Ethernet question

under-score, 2024-10-30:
great device. Can I attach an ethernet/USB C adapter and use  incoming PTZ commands for motor movements?

joshr120, 2024-10-30:
It may be technically possible but probably not very feasible. The ESP32 would need to act as USB host and you would need to write drivers for the specific USB-Ethernet chip.
You would also need some sort of UDB PD power injector to power the stepper driver at the same time.

Closed 2024-10-31.

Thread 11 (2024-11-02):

Suggestion to add caution for installation when not using heat spreader

jgueydan, 2024-11-02:
It might seem obvious to most, but you may want to add a caution in your Read Me description that if someone purchases the standard kit (without heat spreader) that they SHOULD use either spacers or other insulated material between the PD Stepper and the motor body to keep from shorting out the board.  Can't say enough about how much I love this board and it's endless possibilities for use!!  Very well done Josh!!  I'm not a programmer at all, so the included default firmware is great for testing and I very much appreciate it, plus the examples you provided in the software section.

joshr120, 2024-11-04:
I am in the process of creating some more in depth assembly instructions so will be sure to include a note about it. Thanks for pointing it out.

Closed 2024-11-17.

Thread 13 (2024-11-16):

Can you make a new Yaml using this custom component please

wshankles, 2024-11-16:
https://github.com/slimcdk/esphome-custom-components/tree/master/esphome/components/tmc2209

joshr120, 2024-11-17:
This is being worked on should be released shortly

joshr120, 2024-11-17:
New .yaml files have been added to the [ESPHome folder](https://github.com/joshr120/PD-Stepper/tree/main/Software/ESPHome) using the custom [TMC2209 component](https://github.com/slimcdk/esphome-custom-components/tree/master/esphome/components/tmc2209) thanks to @slimcdk

Let me know how you get on

Closed 2024-12-05.

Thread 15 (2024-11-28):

arduino fails to compile

amauryverschooren, 2024-11-28:
https://github.com/joshr120/PD-Stepper/blob/614ef368d68fe608b0ca06e0aee6fc43efc8a80e/Software/PD_Stepper_Web_Server/PD_Stepper_Web_Server.ino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

https://github.com/joshr120/PD-Stepper/blob/614ef368d68fe608b0ca06e0aee6fc43efc8a80e/Software/PD_Stepper_Web_Server/PD_Stepper_Web_Server.ino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

these 2 lines should have const before them.

joshr120, 2024-11-30:
Have you modified the code at all? Seems to compile fine for me in both Arduino IDE 1 and 2

joshr120, 2025-01-09:
I have done some testing and found it likely comes from using the wrong ESPAsyncWebServer library.

I replicated the error when using a fork of the original library: [https://github.com/mathieucarbou/ESPAsyncWebServer](https://github.com/mathieucarbou/ESPAsyncWebServer)
Compiles fine using the original library: [https://github.com/me-no-dev/ESPAsyncWebServer](https://github.com/me-no-dev/ESPAsyncWebServer)

I suggest either change libraries or add const to lines 281 and 292 as @amauryverschooren suggested

Let me know how you get on

amauryverschooren, 2025-01-09:
Hi Josh

Switching to the other library fixed it for me!

Thanks for the help!

Closed 2025-01-09.

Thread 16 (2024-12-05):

What is the AUX connector?

pvince, 2024-12-05:
What type of connector is the AUX connector?

I was looking at adding a contact sensor and wanted to know what kind of crimper // connectors I will need to buy.

joshr120, 2024-12-05:
The AUX connector is a 3 pin JST SH connector. Genuine crimpers can be quite expensive but plenty of places also sell pre-crimped leads: https://www.adafruit.com/product/5765

pvince, 2024-12-05:
Thanks! Could you update the documentation somewhere with that information? (That it is a 3 pin JST SH connector)

joshr120, 2024-12-07:
Will do!

Closed 2024-12-07.

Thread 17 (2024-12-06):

YouTube link is broken

poptix, 2024-12-06:
Your YouTube link in the README.md links to https://www.youtube.com/@ThingsbyJosh-bg9cv which 404's, should be https://www.youtube.com/@ThingsbyJosh

Thanks for the awesome products, mine arrived today!

joshr120, 2024-12-07:
Thanks for pointing that out all fixed now. Hope you find a good use for the board!

Closed 2024-12-07.

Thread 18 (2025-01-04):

[Question] Can I power the module with 12V dc?

schmelly, 2025-01-04:
Dear Josh,

maybe a slightly dumb question but I can I power the module with a 12V dc supply instead of a usb-pd supply?

Background: I intend to use the module to drive a stepper motor for autofocusing an astrophotography setup. Here, typical supply voltages are 12V dc and an approriate connector would be available already in my setup.
If a dc supply won't work this wouldn't be a problem either. I just would have to route an additional usb-c cable to my telescope which would be just a bit more inconvenient.

Thanks and best regards, David

joshr120, 2025-01-04:
Hi David,

There are solder pads on the underside of the PCB where you can directly connect a DC supply of upto 20V.
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

Just make sure you do do not have both the USB and DC power connected at the same time.

Thanks,
Josh

schmelly, 2025-01-05:
Thanks for your prompt support Josh! :-)

Best regards, David

Closed 2025-01-05.

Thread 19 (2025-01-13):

Please document motor current limits

dwmw2, 2025-01-13:
Thanks for this project; it's great. I've just received three of them.

I'm trying to understand the current settings, so I can hook them up to my (2.4V 1.5A 1.6Ω) stepper motors. I was hoping to find something about that in the QuickStart documentation.

Trying to work it out for myself... you have external 100mΩ resistors on BRA/BRB for Rsense. So according to the table in §8 of the TMC2209 datasheet, that gives a max RMS current of 1.92A, when the VREF input is >=2.5V and IRUN is 31.

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

I think the 'current percentage' in the web interface corresponds to IRUN, with 100% mapping to the value 31.

And it looks like the R10 potentiometer allows me to scale VREF from about zero to 2.5V, and you ship it set in the middle, which should mean 100% is 0.96A?
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

So for a 1.5A motor I can either set R10 to its maximum _(or clear GCONF.i_scale_analog which has the same effect?)_ and configure the PD Stepper for 78% (25/32), or actually try to precisely set R10 to give me a VREF of 1.95V?

Without putting probes on the board there's no way to actually read what I've set R10/VREF to, is there?

dwmw2, 2025-01-13:
Hm, doesn't clearing GCONF.i_scale_analog mean VREF is ignored... and doesn't the TMC2209 component do exactly that? https://github.com/slimcdk/esphome-custom-components/blob/master/esphome/components/tmc2209/tmc2209_component.cpp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

Does that mean VREF from R10 is ignored in the software that's shipped by default?

slimcdk, 2025-01-13:
> clearing GCONF.i_scale_analog mean VREF is ignored...

Correct. VREF is ignored with `I_scale_analog = 0` and current scaling is controlled through `IRUN` and `IHOLD` registers via the [`tmc2209.currents`](https://github.com/slimcdk/esphome-custom-components/tree/master/esphome/components/tmc2209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) action. `I_scale_analog=1` will use VREF and ignore values in said registers. You can overrule that initial setting by [writing to the register](https://github.com/slimcdk/esphome-custom-components/tree/master/esphome/components/tmc2209#advanced) from an `on_boot` action, if you wish to experiment.

Having the input on VREF for a hardware project like this adds more flexibility for the end user. Anyway, feel free to open a ticket on my project for further discussion on adding in this configuration option.

dwmw2, 2025-01-13:
> `I_scale_analog=1` will use VREF and ignore values in said registers.

Hm, is that true? I thought `IRUN` and `IHOLD` were still applicable whether `I_scale_analog` is set or not.
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

> You can overrule that initial setting by [writing to the register](https://github.com/slimcdk/esphome-custom-components/tree/master/esphome/components/tmc2209#advanced) from an on_boot action, if you wish to experiment.

Your docs tell me that doing that may cause instability in the ESPHome component and should be avoided :)
It also looks like you have a `CONF_ANALOG_SCALE` defined in the config already; I'm just not sure it's wired up.

In fact I don't think I *want* to use VREF, as I have no simple way of measuring what I've set it to. For now I'm just trying to understand how to set the thing up. I *think* that it's configured to ignore VREF by default, so I should just set the current percentage to 70% and that should do the right thing.

dwmw2, 2025-01-13:
Ah, the software on the device as it's shipped isn't ESPHome; it's [this](https://github.com/joshr120/PD-Stepper/tree/main/Software/PD_Stepper_Web_Server) one which uses https://github.com/janelia-arduino/TMC2209. So maybe VREF *is* applicable to the device as it's shipped? So I should probably turn it to max and then set IRUN to 70% (and check it doesn't catch fire).

joshr120, 2025-01-15:
My understanding it that in both the default webserver case as well as when using ESPHome with the component by @slimcdk I_scale_analog is set to 0 and the VREF is ignored.

I have verified for both cases by adjusting the potentiometer to it's extremes and feeling no difference in the force required to stall the motor.

I will update the getting started guide with a bit more info on how to select the current. I may also update the webserver to give values in the drop down instead of a percentage.

As a side note if you do want to measure VREF there is a test point on the underside of the board.

dwmw2, 2025-01-15:
Thanks! The dropdowns in the webserver probably shouldn't be in multiples of 10% either, should they? Each step in `IRUN` is actually about 0.06A, so the options are:

 - 3% / 60mA
 - 6% / 120mA
 - 9% / 180mA
 - 12% / 240mA
 - 15% / 300mA
 - 18% / 360mA
 - 21% / 420mA
 - 25% / 480mA
 - 28% / 540mA
 - 31% / 600mA
 - 34% / 660mA
 - 37% / 720mA
 - 40% / 780mA
 - 43% / 840mA
 - 46% / 900mA
 - 50% / 960mA
 - 53% / 1.02A
 - 56% / 1.08A
 - 59% / 1.14A
 - 62% / 1.20A
 - 65% / 1.26A
 - 68% / 1.32A
 - 71% / 1.38A
 - 75% / 1.44A
 - 78% / 1.50A
 - 81% / 1.56A
 - 84% / 1.62A
 - 87% / 1.68A
 - 90% / 1.74A
 - 93% / 1.80A
 - 96% / 1.86A
 - 100% / 1.92A

That's not taking a 10% safety margin into account, and it's assuming all current values are in RMS not peak. For my 1.5A motor (which I'm assuming is 1.5A RMS) I'll choose the 71% option, `IRUN=0x16`.

dwmw2, 2025-01-15:
> As a side note if you do want to measure VREF there is a test point on the underside of the board.

Could that be run to an ADC input pin on the ESP32? Or would that cause too much noise?

joshr120, 2025-01-16:
It probably could be fed into an ADC but as it is disabled for most use cases probably not worth it

slimcdk, 2025-02-13:
I spend a bit of time investigating this further (while also adding the option [`analog_current_scale`](https://github.com/slimcdk/esphome-custom-components/blob/master/esphome/components/tmc2209/README.md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) to set `I_scale_analog` for the ESPHome component) and has now concluded the following.

* `I_scale_analog=0`  ignores any input from VREF and solely scale currents from what is set in IRUN register.
* `I_scale_analog=1` appear to take both VREF _and_ IRUN into account such that VREF scales from 0 to what is in the register. So, VREF at 2.5V is equal to what is set in the register.

Have you tested this and could perhaps confirm my experience? This is not the behavior I understand from reading the docs.

dwmw2, 2025-02-13:
I think that *was* the behaviour I understand from reading the docs, as cited in https://github.com/joshr120/PD-Stepper/issues/19#issuecomment-2587626229 above?

slimcdk, 2025-02-13:
Maybe I read it wrong, but I interpret the docs (and your comment) as "VREF determines the scaling of IRUN" rather than "VREF scales _up to_ IRUN", if that makes any sense. I would argue there is a key distinction here: in the latter case, VREF alone couldn't set full current unless IRUN is at its maximum (31). In contrast, if VREF directly scales the current, it could do so regardless of IRUN's value. That’s why I originally argued that `I_scale_analog` configured either VREF or IRUN scaling determines the current, but what I've later experienced isn't the case. Perhaps you can find time to replicate what I've experienced?

Anyway, I don't think VREF should be used, unless there is a setup where the hardware was specifically designed for it, which isn't the case in this project.

slimcdk, 2025-02-13:
Yep, in either case IRUN will always scale the current. If `I_scale_analog=1`, then VREF adds onto that.

Closed 2025-03-27.

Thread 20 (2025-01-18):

Help With Stemma

Phando, 2025-01-18:
Is there an example of using a rotary via the stemma connector?
Do I need to set up the stemma pins in my platformio project? If so, what pins are used in the stemma connector.
Is there a platformio board definition for the Esp32-S3-PDStepper?

Thank you!

joshr120, 2025-01-18:
For rotary encoder examples this will very much depend on what module/device you are connecting to it so there are not any examples as part of this project. You will want to refer to the module you are using as to how to use it.

The STEMMA QT connector uses I2C and the pins are as follows:
```
#define SCL     9
#define SDA     8
```

This is already setup in most of the examples as it is on the same bus as the built in AS5600 encoder.

There is not a custom board definition for the PD Stepper but you should just be able to use a generic ESP32-S3 dev board if you would like.

Phando, 2025-01-18:
Thanks for the quick reply! I  using the adafruit led rotary encoder. I’ll check more examples.On Jan 18, 2025, at 2:16 PM, joshr120 ***@***.***> wrote:
For rotary encoder examples this will very much depend on what module/device you are connecting to it so there are not any examples as part of this project. You will want to refer to the module you are using as to how to use it.
The STEMMA QT connector uses I2C and the pins are as follows:
#define SCL     9
#define SDA     8

This is already setup in most of the examples as it is on the same bus as the built in AS5600 encoder.
There is not a custom board definition for the PD Stepper but you should just be able to use a generic ESP32-S3 dev board if you would like.

—Reply to this email directly, view it on GitHub, or unsubscribe.You are receiving this because you authored the thread.Message ID: ***@***.***>

Closed 2025-02-11.

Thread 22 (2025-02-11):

Reverse voltage protection

dwmw2, 2025-02-11:
With the stepper PCB unpowered, if I pull the blind cord manually the motor appears to provide power and the green LED lights up.

With the stepper PCB  powered but idle (in freewheeling mode), the board seems to crash if I pull the blind cord manually above a certain speed.

With the stepper PCB powered from my laptop... my laptop now appears to be completely dead and won't power up at all any more

joshr120, 2025-02-11:
Stepper motors generate back EMF when being back driven and act as a generator. This is very common and devices with stepper motors such as 3D printers should never be back driven too fast. The PD stepper is no exception to this.

Some servo motors will have a braking resistor to soak up some of this generated energy. A large TVS diode on the power rail can also help with shorter spikes but will only be so effective for a continuous reverse power generation.

If the back EMF is over 22V then the buck converter may not longer be able to effectively regulate the 3V3 rail. This is likely what is causing the board to crash in your second scenario once the motor reaches a certain speed.

I will add more warning notes throughout the documentation not to back drive the motor quickly. This is especially the case when a computer is connected, in general a motor should not be spun when powered from a computer (The Arduino sketches all disable the stepper driver unless powered via PD to avoid drawing too much current from a computer).

If you have blown up a motor board let me know and I can send out a new one.

dwmw2, 2025-02-11:
Is it possible to gate the connections from the motor to the TMC2209 with MOSFETs, so they're only connected when it's actually trying to *drive* the motor?

I think the board is OK, but anyway you've already sent me a spare motor board, thanks! I just ordered a fourth so I have a spare, after noticing that one of my first three has one of the buttons missing (probably from my repeated assembly/disassembly of 3D mount parts).

I'm more worried about the laptop at this point. :)

Arguably *it* should have better protection on its USB port too.

Could the PD stepper board at least have a diode to prevent killing whatever is on the USB port? If the stepper PCB itself dies that's slightly less of an issue.

dwmw2, 2025-02-11:
FWIW I managed to recover the laptop after a few attempts to reset it.

dwmw2, 2025-02-11:
Would setting the tmc2209 `standstill_mode: coil_short_ls` help, at least in the case where the board is powered?

If not, assuming the back EMF is coming through VBUS from the tmc2209 wouldn't it be possible to put a diode there to prevent it feeding back to either the buck converter or the USB connector?

I'd probably be inclined to put *another* diode between the buck converter and the USB connector, for the case where power is being fed to the pads on the underside of the board, if we can stand the voltage drop.

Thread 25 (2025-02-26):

Improve WiFi connectivity

dwmw2, 2025-02-26:
The issue I've been having with MQTT latency ultimately occurs because of poor WiFi connectivity. Even on my desk, the PD-stepper seems to have less reliably connectivity than other similar ESP32 boards. I've noticed they all have a cut-out of the PCB behind the antenna, while the PD-stepper doesn't. Perhaps that would improve connectivity, and thus improve the MQTT performance too?

https://www.reddit.com/r/esp32/comments/xszr9g/esp32_pcb_antenna_test_results/

joshr120, 2025-02-27:
The design of the PD stepper is obviously very space constrained would be nice to have the ideal 15mm clearance around the antenna but this is not very feasible. There are cutouts in the copper underneath the antenna to try and minimize any unintended changes in impedance on the antenna. There are certainly a lot of other boards that take this same approach:
[https://www.adafruit.com/product/5900](https://www.adafruit.com/product/5900)
[https://www.sparkfun.com/sparkfun-thing-plus-esp32-wroom-usb-c.html](https://www.sparkfun.com/sparkfun-thing-plus-esp32-wroom-usb-c.html)
[https://www.dfrobot.com/product-2837.html?srsltid=AfmBOoqDtr-pjgXty1KHIvRVxYn3SfexMLbfoA4175G_c9lSPYz_nvoT](https://www.dfrobot.com/product-2837.html?srsltid=AfmBOoqDtr-pjgXty1KHIvRVxYn3SfexMLbfoA4175G_c9lSPYz_nvoT)
etc.

Closed 2025-03-04.

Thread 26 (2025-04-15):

ESPHome reverts to base settings after power cycle

inclementweather, 2025-04-15:
Hello,
I'm having a bit of trouble with my PDSteppers.  To set them up initially I flashed them with ESPHome base build from https://web.esphome.io/?dashboard_wizard, then adopted into HA/ESPHome.  After that I copy the advanced blinds config from this repo to the builder interface for the device, compile then flash over Wifi.

Everything works fine after the flashing process.  I can control the stepper from my HA interface.  However if I remove power and plug it back in it appears to revert back to the initial image I flashed from esphome.io.

Any idea what might be happening?

joshr120, 2025-04-16:
Hi, when you say it "appears to revert back to the initial image" what exactly is happening which indicates this?

Additionally, have you tried flashing over USB instead of WiFi?

inclementweather, 2025-04-16:
After the power cycle the ESP appears as online but no longer reports any attributes or settings.  If I check the logs over WiFi it only shows the connection to WiFi being established.  All the normal output from the configured firmware is absent. I can manually turn the stepper and there's no messages about the rotation, no reporting of voltage, etc.

I only flashed the initial ESPHome firmware over USB but not the configured firmware. I can try doing that later today.

joshr120, 2025-04-16:
Sounds very similar to this problem which was solved by setting a static IP
https://www.reddit.com/r/Esphome/comments/117x87n/first_esp_device_having_to_reinstall_after_every/

inclementweather, 2025-04-17:
Weird, that was exactly the problem but I'm still not sure why.  Maybe conflicting names stored in home assistant?

Closed 2025-04-17.

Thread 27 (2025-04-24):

Problem request

mmpzhennan, 2025-04-24:
Hello, I encountered some issues during the process of reproducing this project. After completing the hardware soldering, there was no response when connecting to the computer's USB via type-c. The port of the arduino was gray. Is this a driver problem or a hardware issue?

joshr120, 2025-04-24:
Hi, bit hard to diagnose your problem without more information.

To start does the 3.3V LED turn on when power is connected?

And what do you mean by "The port of the arduino was gray"?

mmpzhennan, 2025-04-25:
Hello, I have completed this issue. It was caused by my welding process. When I re-welded, the computer could recognize the USB. Thank you very much for your reply

Closed 2025-04-25.

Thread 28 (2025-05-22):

Serial Commands over USB-C

nirokato, 2025-05-22:
Hello,

Thank you for creating such a great platform. It's so cool!

On to the issue:
> Serial commands can be sent/received through the USB-C connector (Note if your device sending the commands cannot provide enough power you may need an injector of some kind)

I went through as much of the documentation as possible, and I couldn't really find anything about actually sending commands over usb-c.

Setup:
I'm successfully powering the pd-stepper using a Pixel 8 Pro's OTG (pd-stepper set to 5V, 30% max current) and using [Serial USB Terminal](https://play.google.com/store/apps/details?id=de.kai_morich.serial_usb_terminal&pcampaignid=web_share) to view logging output:

Here's the pd-stepper web settings:
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

Here's the Serial USB Terminal interaction, keep in mind the slider was set to Snap Centre:
```
21:36:59.286 Connected to CDC device
21:36:59.292 Code Starting
21:36:59.292 AP IP address: 192.168.4.1
21:38:43.202 
21:38:52.612 Slider value: 0
21:38:53.431 Slider value: 207
21:38:53.513 Slider value: 0
21:38:58.570 Slider value: 207
21:38:58.657 Slider value: 0
21:38:59.289 Slider value: 207
21:38:59.377 Slider value: 0
21:39:14.465 help
21:48:24.384 h
21:48:26.615 ?
21:48:32.983 status
21:48:36.996 info
21:48:41.961 Disconnected
21:48:43.129 Connected to CDC device
21:48:43.129 Build:Mar 27 2021
21:48:58.693 a
21:49:00.038 ab
21:49:02.008 b
```
As you can see, I blindly sent commands and didn't receive any output from the pd-stepper.

What is a hardware newb like me to do next?

Thank you!

joshr120, 2025-05-22:
Hi,
Cool idea to connect it directly to a phone! Currently none of the examples have been setup to receive serial commands. You would need to modify one of the examples to respond to your commands.

However, I am currently working on a USB hub with USB PD on the downstream (device) ports which will allow serial control. As part of this I will be adding a serial control example.

Matoseb, 2025-07-05:
Hi, I'm not sure why I can't receive any Serial messages when I'm simply connected to my macbook via USB-C. I'm running a basic Serial sketch, with small delays before Serial.begin. But I can't receive any messages.
Am I missing something?

Matoseb, 2025-07-05:
> Hi, I'm not sure why I can't receive any Serial messages when I'm simply connected to my macbook via USB-C. I'm running a basic Serial sketch, with small delays before Serial.begin. But I can't receive any messages. Am I missing something?

Got it! In the board settings in Arduino, USB CDC On Boot must be set to "Enabled"

Matoseb, 2025-08-01:
> However, I am currently working on a USB hub with USB PD on the downstream (device) ports which will allow serial control. As part of this I will be adding a serial control example.

Would this usb hub allow to safely flash the esp32 while it has external power connected to its vbus solder pad?

joshr120, 2025-08-02:
Even with the custom hub, the board should never be externally powered by the VBUS solder pads and connected to USB at the same time.
If you absolutely needed to, you could cut open a USB cable and disconnect the red VBUS wire inside the cable.

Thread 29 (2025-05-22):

Compiling error |   EEPROM

emgiorzan, 2025-05-22:
Dear Josh,
On compiling, PD_Stepper_Web_Server.ino I get this error:

 PD_Stepper_Web_Server_ino_copy22_May.ino: In function 'void setup()':
C:\Arduino_IDE\DRONE_CODING\PD_Stepper_Web_Server_ino_copy22_May\PD_Stepper_Web_Server_ino_copy22_May.ino:223:4: error: 'readSettings' was not declared in this scope
  223 |    readSettings(); //get saved values from

Any information regarding this error would be appreciated. THanks

emgiorzan, 2025-05-23:
My apologies for the cascading messages,
The actuator will actually operate with the pre-installed software,
Trying to compile and upload examples' code so that adjust them, for example showing angle in degrees or use step/dir functions  and "learn" by configuring is what I try to do...

Is there a guide for that ? Or a tip on how to start ? (What did was to install the arduino ide, update the configurations, use the ones given on your site page, and then "copy" "paste" the software code on a sketch.
Thanks in advance.

emgiorzan, 2025-05-23:
The first issue was part of arduino IDE setup. All fixed and worked through aforementioned resolved issues. Thanks! Good job!

Closed 2025-05-23.

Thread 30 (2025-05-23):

No access point is created

emgiorzan, 2025-05-23:
Hi all,

After successfully uploading the code provided @https://github.com/joshr120/PD-Stepper/tree/main/Software/PD_Stepper_Web_Server

I reset the module and LED4 stays green while LED3 is blinking.

On my laptop I cannot see any access point..

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

Any suggestions?

joshr120, 2025-05-24:
Hi, if LED 3 is blinking this seems like a USB PD power/negotiation issue.

Some more info would probably help. How are you powering the board? do you have a motor plugged in etc.

Before uploading the code yourself did you manage to connect to the webserver with the pre-installed code?

emgiorzan, 2025-05-24:
Unfortunately I am not able to test it today. Possible back on it on Sunday
or Monday. Is there a way to reset it?

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

joshr120, 2025-05-24:
Does not necessarily sounds like a software issue. You can  however force it into bootloader mode by holding down the BOOT button, pressing RST and then releasing BOOT. You can then re-flash the firmware. The firmware you have loaded should be exactly the same as what was shipped on it.

joshr120, 2025-05-25:
Very hard to know without more information. I would first try with disconnecting the motor and a different power supply.

emgiorzan, 2025-05-26:
Thanks,
After checking the board alone, it will compile and run, but for the motor,
I have a faulty adaptor and not enough voltage to operate the motor.

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

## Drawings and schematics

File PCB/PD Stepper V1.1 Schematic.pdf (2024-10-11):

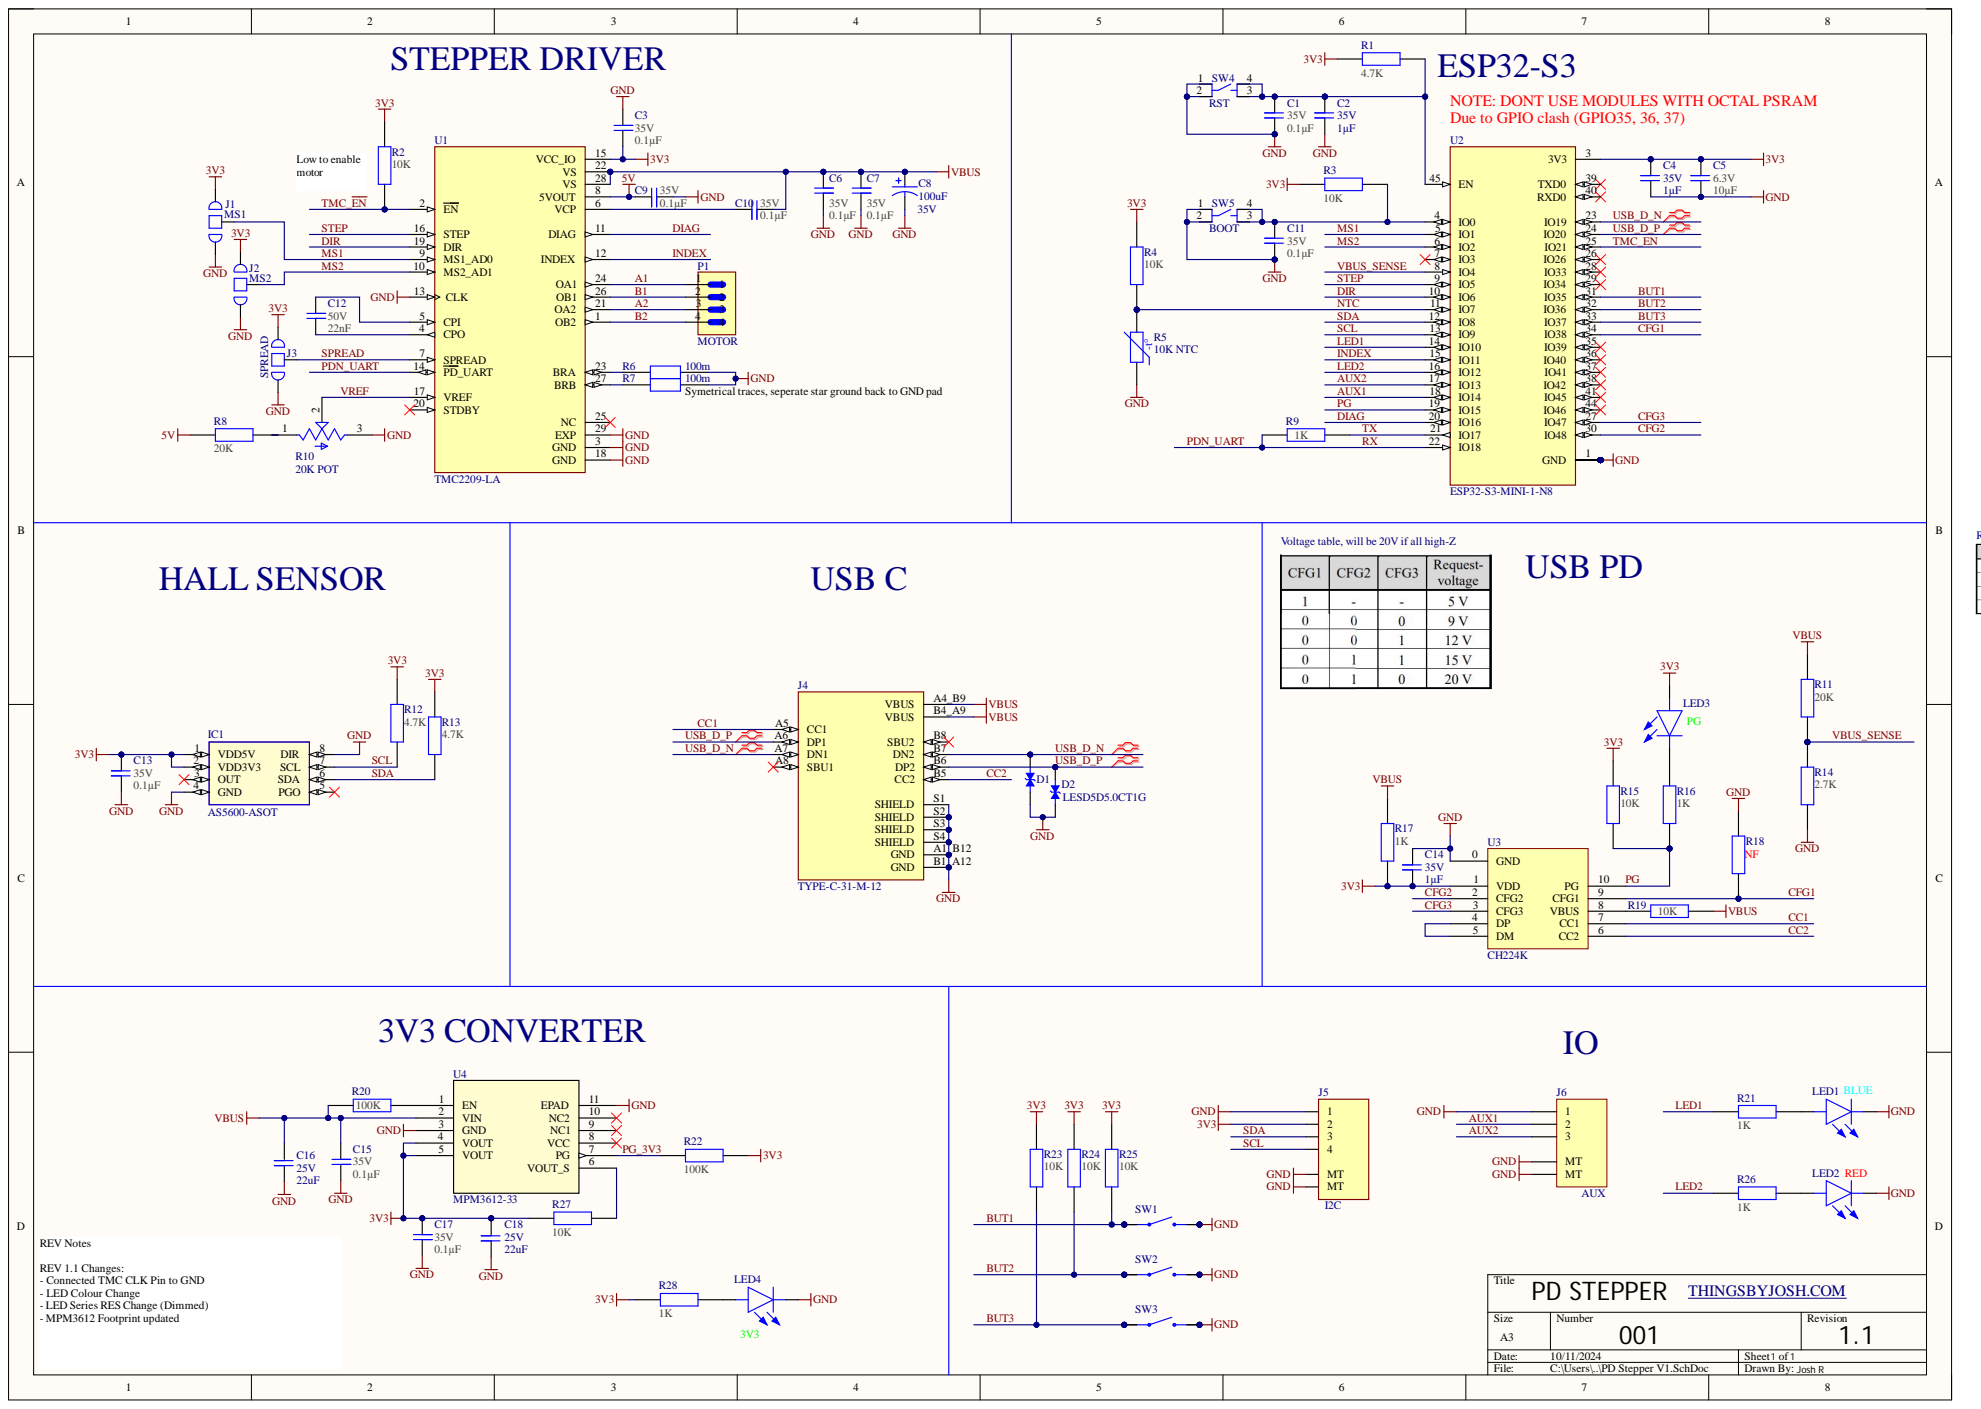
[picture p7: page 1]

NOTE: DONT USE MODULES WITH OCTAL PSRAM
Due to GPIO clash (GPIO35, 36, 37)

Symetrical traces, seperate star ground back to GND pad

RES (to GND) table for if CFG2, CFG3 are not used & NC Voltage table, will be 20V if all high-Z

REV 1.1 Changes:
- Connected TMC CLK Pin to GND
- LED Colour Change
- LED Series RES Change (Dimmed)
- MPM3612 Footprint updated

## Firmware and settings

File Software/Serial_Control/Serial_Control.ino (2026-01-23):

/*
 * PD Stepper Serial Control Example
 * * Modified to support Serial commands on USB (Serial) 
 * and AUX1/AUX2 pins (Serial1).
 */

#include <TMC2209.h> //  https://github.com/janelia-arduino/TMC2209/tree/main
#include <Preferences.h> //for saving to flash (instead of old EEPROM lib)
#include <Wire.h> //For I2C for encoder

Preferences preferences;

//TMC2209 setup
TMC2209 stepper_driver;
HardwareSerial & serial_stream = Serial2;
const long SERIAL_BAUD_RATE = 115200;

const uint8_t RUN_CURRENT_PERCENT = 20; //how much current to run at (0-100%)

//TMC2209 Stepper Driver
#define TMC_EN  21
#define STEP    5
#define DIR     6
#define MS1     1
#define MS2     2
#define SPREAD  7
#define TMC_TX  17
#define TMC_RX  18
#define DIAG    16
#define INDEX   11

//PD Trigger (CH224K)
#define PG      15  //power good singnal (dont enable stepper untill this is good)
#define CFG1    38
#define CFG2    48
#define CFG3    47

//Other
#define VBUS    4
#define NTC     7
#define LED1    10
#define LED2    12
#define SW1     35
#define SW2     36
#define SW3     37
#define AUX1    14
#define AUX2    13

//Global variables
int set_speed = 0;
bool PGState = 0; 
bool enabledState = 0;
bool state = 0; 

//AS5600 Hall Effect Encoder
#define AS5600_ADDRESS 0x36 
signed long total_encoder_counts = 0;
double angle = 0; 
int encoder_offset = 0; 

unsigned long lastEncRead = 0;
int mainFreq = 50; 

//button read and debounce
bool incButtonState = HIGH;
bool decButtonState = HIGH;
bool resetButtonState = HIGH;
unsigned long lastDebounceTime = 0;
unsigned long debounceDelay = 50;
int buttonSpeed = 0;

//Voltage reading and calc
float VBusVoltage = 0;
float VREF = 3.3;
const float DIV_RATIO = 0.1189427313;  

//Default values
bool enabled1 = 1;
int setVoltage = 12;
int microsteps = 64;
int current = 20;
int stallThreshold = 10;
String standstillMode = "NORMAL";
float positionSpeed = 360;
int stepsPerRev = 200;
String closedLoopType = "MOVE_FROM_ENC";
bool mappingDirection = 1;
bool verboseOutput = 1;

//Variables for position control
signed long setPoint = 0;
signed long CurrentPosition = 0;
unsigned long lastStep = 0;
signed long microsteps_to_move = 0;

// Forward Declarations
void readSerialCommands(Stream &port);
unsigned long getStepDelay(float deg_per_sec, int steps_per_rev, int microsteps);
void readEncoder();
void configureSettings();
void readSettings();
void writeSettings();

void setup() {
  //PD Trigger Setup
  pinMode(PG, INPUT);
  pinMode(CFG1, OUTPUT);
  pinMode(CFG2, OUTPUT);
  pinMode(CFG3, OUTPUT);
  digitalWrite(CFG1, LOW);  
  digitalWrite(CFG2, LOW);  
  digitalWrite(CFG3, HIGH); 

  //General
  pinMode(SW1, INPUT);
  pinMode(SW2, INPUT);
  pinMode(SW3, INPUT);
  pinMode(LED1, OUTPUT);
  pinMode(LED2, OUTPUT);
  pinMode(STEP, OUTPUT);
  pinMode(DIR, OUTPUT);

  //Setup serial comms with TMC2209
  pinMode(MS1, OUTPUT);
  pinMode(MS2, OUTPUT);
  pinMode(TMC_EN, OUTPUT);
  pinMode(DIAG, INPUT);
  digitalWrite(TMC_EN, LOW); 

  digitalWrite(MS1, LOW); 
  digitalWrite(MS2, LOW);

  //AS5600 Hall Encoder Setup
  Wire.begin(SDA, SCL);  

  readSettings(); 
  
  stepper_driver.setup(serial_stream, SERIAL_BAUD_RATE, TMC2209::SERIAL_ADDRESS_0, TMC_RX, TMC_TX);
  stepper_driver.setRunCurrent(RUN_CURRENT_PERCENT);
  stepper_driver.enableAutomaticCurrentScaling(); 
  stepper_driver.enableStealthChop(); 
  stepper_driver.setCoolStepDurationThreshold(5000); 
  stepper_driver.disable();

  configureSettings(); 

  readEncoder();
  encoder_offset = total_encoder_counts;

  delay(200); 
  
  // USB Serial
  Serial.begin(115200);
  
  // AUX Serial (Serial1) on AUX1 (TX) and AUX2 (RX)
  // Note: Ensure correct TX/RX logic for your external device
  Serial1.begin(115200, SERIAL_8N1, AUX2, AUX1); 

  digitalWrite(LED1, HIGH); 
  delay(200);
  digitalWrite(LED1, LOW);  
}

void loop() {
  // Check USB Serial
  if (Serial.available()) {
    readSerialCommands(Serial);
  }

  // Check AUX Serial
  if (Serial1.available()) {
    readSerialCommands(Serial1);
  }

  if (millis() - lastEncRead >= mainFreq){ 
    lastEncRead = millis();
    readEncoder(); 

    digitalWrite(LED2, digitalRead(DIAG)); 

    PGState = digitalRead(PG); 
    if (PGState == LOW and enabled1 == 1 and enabledState == 0){ 
      stepper_driver.enable();
      enabledState = 1;
    } else if ((PGState == HIGH or enabled1 == 0) and enabledState == 1){ 
      stepper_driver.disable();
      enabledState = 0;
    }
  }

  unsigned long step_delay_us = getStepDelay(positionSpeed, stepsPerRev, microsteps); 
 
  if ((micros()-lastStep > (step_delay_us/2)) and (state == HIGH)){
    state = LOW;
    digitalWrite(STEP, LOW);
  }

  // OPEN LOOP CONTROL
  if (closedLoopType == "OPEN_LOOP"){
    if (setPoint > (CurrentPosition + 256/microsteps)){
      if (micros()-lastStep > step_delay_us){
        digitalWrite(DIR, mappingDirection ? HIGH : LOW);
        state = HIGH;
        digitalWrite(STEP, HIGH);
        CurrentPosition = CurrentPosition + (256/microsteps);  
        lastStep = micros();
      }
    } else if (setPoint < (CurrentPosition - 256/microsteps)){
      if (micros()-lastStep > step_delay_us){
        digitalWrite(DIR, mappingDirection ? LOW : HIGH);
        state = HIGH;
        digitalWrite(STEP, HIGH);
        CurrentPosition = CurrentPosition - (256/microsteps);  
        lastStep = micros();
      }
    }
  } else {
    // MOVE FROM ENCODER
    if (microsteps_to_move >= 256/microsteps){
      if (micros()-lastStep > step_delay_us){
        digitalWrite(DIR, mappingDirection ? HIGH : LOW);
        state = HIGH;
        digitalWrite(STEP, HIGH);
        microsteps_to_move = microsteps_to_move - (256/microsteps);  
        lastStep = micros();
      }
    } else if (microsteps_to_move <= -256/microsteps){
      if (micros()-lastStep > step_delay_us){
        digitalWrite(DIR, mappingDirection ? LOW : HIGH);
        state = HIGH;
        digitalWrite(STEP, HIGH);
        microsteps_to_move = microsteps_to_move + (256/microsteps);  
        lastStep = micros();
      }
    }
  }

  // Button handling
  if ((millis() - lastDebounceTime) > debounceDelay) {
    lastDebounceTime = millis();
    bool currentIncButtonState = digitalRead(SW3);
    bool currentDecButtonState = digitalRead(SW1);
    bool currentResetButtonState = digitalRead(SW2);
  
    if (currentIncButtonState != incButtonState) {
      incButtonState = currentIncButtonState;
      if (incButtonState == LOW) {
        buttonSpeed = min(buttonSpeed + 10, 330);
        stepper_driver.moveAtVelocity(buttonSpeed*(microsteps));
      }
    }
    if (currentDecButtonState != decButtonState) {
      decButtonState = currentDecButtonState;
      if (decButtonState == LOW) {
        buttonSpeed = max(buttonSpeed - 10, -330);
        stepper_driver.moveAtVelocity(buttonSpeed*(microsteps));
      }
    }
    if (currentResetButtonState != resetButtonState) {
      resetButtonState = currentResetButtonState;
      if (resetButtonState == LOW) {
        buttonSpeed = 0;
        stepper_driver.moveAtVelocity(0);
      }
    }
  }
}

void readSerialCommands(Stream &port) {
  String cmd = port.readStringUntil('\n');
  cmd.trim();

  if (cmd.length() == 0) {
    return; // Exit immediately if the line is empty
  }

  if (cmd.startsWith("deg=")) {
    float targetAngle = cmd.substring(4).toFloat();
    setPoint = (targetAngle/360.0) * stepsPerRev * 256; 
    signed long posMicrosteps = (stepsPerRev * 256 * (total_encoder_counts-encoder_offset)) / 4096.0; //gets current pos (should be moved to loop)
    microsteps_to_move = setPoint - posMicrosteps; //not used for open loop control
    if (verboseOutput) {
      port.print("SUCCESS: Target angle set to: ");
      port.println(targetAngle);
    }
    return;
  }
  if (cmd.startsWith("deg_rel=")) {
    float relAngle = cmd.substring(8).toFloat();
    setPoint += (relAngle/360.0) * stepsPerRev * 256; 
    signed long posMicrosteps = (stepsPerRev * 256 * (total_encoder_counts-encoder_offset)) / 4096.0;
    microsteps_to_move = setPoint - posMicrosteps; 
    if (verboseOutput) {
      port.print("SUCCESS: Target angle increased by: ");
      port.println(relAngle);
    }
    return;
  }
  else if (cmd.startsWith("vel=")) {
    float motorSpeed = cmd.substring(4).toFloat();
    int32_t microsteps_per_period = ((motorSpeed/360.0)*stepsPerRev*microsteps)/0.715;
    stepper_driver.moveAtVelocity(microsteps_per_period*-1);
    if (verboseOutput) {
      port.print("SUCCESS: Speed set to: ");
      port.println(motorSpeed);
    }
    return;
  }
  else if (cmd.startsWith("steps_per_rev=")) {
    int stepsPerRevRec = cmd.substring(14).toInt();
    if (stepsPerRevRec == 200 or stepsPerRevRec == 400){
      stepsPerRev = stepsPerRevRec;
      if (verboseOutput) {
        port.print("SUCCESS: Steps per revolution set to: ");
        port.println(stepsPerRev);
      }
      writeSettings();
    } else {
      port.println("ERROR: Steps per revolution must be 200 or 400 ");
    }
    return;
  }
  else if (cmd.startsWith("enable=")) {
    String enableRec = cmd.substring(7);
    if (enableRec == "0" or enableRec == "FALSE" or enableRec == "disabled"){
      enabled1 = 0;
      if (verboseOutput) {port.println("SUCCESS: Driver disabled");}
      writeSettings();
    } else if (enableRec == "1" or enableRec == "TRUE" or enableRec == "enabled"){
      enabled1 = 1;
      if (verboseOutput) {port.println("SUCCESS: Driver enabled");}
      writeSettings();
    } else {
      port.println("ERROR: Enable must be set to 0, 1, FALSE or TRUE");
    }
    return;
  }
  else if (cmd.startsWith("microsteps=")) {
    int microstepsRec = cmd.substring(11).toInt();
    if (microstepsRec == 1 || microstepsRec == 4 || microstepsRec == 8 || microstepsRec == 16 || 
        microstepsRec == 32 || microstepsRec == 64 || microstepsRec == 128 || microstepsRec == 256){
      microsteps = microstepsRec;
      writeSettings();
      if (verboseOutput) {
        port.print("SUCCESS: Microsteps set to: ");
        port.println(microsteps);
      }
    } else {
      port.println("ERROR: microsteps must be 1, 4, 8, 16, 32, 64, 128 or 256");
    }
    return;
  }
  else if (cmd.startsWith("voltage=")) {
    int setVoltageRec = cmd.substring(8).toInt();
    if (setVoltageRec == 5 || setVoltageRec == 9 || setVoltageRec == 12 || setVoltageRec == 15 || setVoltageRec == 20){
      setVoltage = setVoltageRec;
      if (verboseOutput) {
        port.print("SUCCESS: PD Voltage set to: ");
        port.println(setVoltage);
      }
      writeSettings();
    } else {
      port.println("ERROR: Voltage must be 5, 9, 12, 15 or 20");
    }
    return;
  }
  else if (cmd.startsWith("current=")) {
    int currentRec = cmd.substring(8).toInt();
    if (currentRec >= 0 and currentRec <= 100){
      current = currentRec;
      if (verboseOutput) {
        port.print("SUCCESS: Current set to: ");
        port.print(current);
        port.println("%");
      }
      writeSettings();
    } else {
      port.println("ERROR: Current needs to be a value from 0-100");
    }
    return;
  }
  else if (cmd.startsWith("speed=")) {
    float speedRec = cmd.substring(6).toFloat();
    if (speedRec >= 0 and speedRec <= 5000){
      positionSpeed = speedRec;
      if (verboseOutput) {
        port.print("SUCCESS: Position speed value set to: ");
        port.println(positionSpeed);
      }
      writeSettings();
    } else {
      port.println("ERROR: Position speed must be between 0 and 5000 deg/s");
    }
    return;
  }
  else if (cmd.startsWith("standstill_mode=")) {
    String standstillModeRec = cmd.substring(16);
    if (standstillModeRec == "NORMAL" || standstillModeRec == "FREEWHEELING" || 
        standstillModeRec == "BRAKING" || standstillModeRec == "STRONG_BRAKING"){
      standstillMode = standstillModeRec;
      if (verboseOutput) {
        port.print("SUCCESS: Standstill mode set to: ");
        port.println(standstillMode);
      }
      writeSettings();
    } else {
      port.println("ERROR: Standstill mode must be NORMAL, FREEWHEELING, BRAKING or STRONG_BRAKING");
    }
    return;
  }
  else if (cmd.startsWith("closed_loop_type=")) {
    String closedLoopTypeRec = cmd.substring(17);
    if (closedLoopTypeRec == "OPEN_LOOP" || closedLoopTypeRec == "MOVE_FROM_ENC" || closedLoopTypeRec == "CLOSED_LOOP"){
      closedLoopType = closedLoopTypeRec;
      if (verboseOutput) {
        port.print("SUCCESS: Closed loop mode set to: ");
        port.println(closedLoopType);
      }
      writeSettings();
    } else {
      port.println("ERROR: MOVE_FROM_ENC must be OPEN_LOOP, MOVE_FROM_ENC Or CLOSED_LOOP");
    }
    return;
  }
  else if (cmd.startsWith("mappingDirection=")) {
    int mappingDirectionRec = cmd.substring(17).toInt();
    if (mappingDirectionRec == 0 or mappingDirectionRec == 1){
      mappingDirection = mappingDirectionRec;
      if (verboseOutput) {
        port.print("SUCCESS: Mapping direction mode set to: ");
        port.println(mappingDirection);
      }
      writeSettings();
    } else {
      port.println("ERROR: Mapping direction must be 0 or 1");
    }
    return;
  }
  else if (cmd.startsWith("verboseOutput=")) {
    String verboseOutputRec = cmd.substring(14);
    if (verboseOutputRec == "0" or verboseOutputRec == "FALSE" or verboseOutputRec == "disabled"){
      verboseOutput = 0;
      writeSettings();
    } else if (verboseOutputRec == "1" or verboseOutputRec == "TRUE" or verboseOutputRec == "enabled"){
      verboseOutput = 1;
      port.println("SUCCESS: verbose output enabled");
      writeSettings();
    } else {
      port.println("ERROR: verbose output must be set to 0, 1, FALSE or TRUE");
    }
    return;
  }
  else if (cmd.equalsIgnoreCase("HELP")) {
    port.println("\nList of available commands:");
    port.println("deg= xxx.x          : move to position, in degrees");
    port.println("deg_rel= xxx.x      : relative move to position, in degrees");
    port.println("vel= xxxx           : spin at set velocity");
    port.println("steps_per_rev= xxx  : Steps per revolution, 200 or 400");
    port.println("enable= x           : enable/disable driver, 0 or 1");
    port.println("microsteps= xxx     : set microsteps, 1, 4, 8, 16, 32, 64, 128, 256");
    port.println("voltage= xx         : set USB PD Voltage, 5, 9, 12, 15 or 20");
    port.println("current= xxx        : set driver current %, 0-100");
    port.println("speed= xxxx         : set position speed deg/s, 0-5000");
    port.println("standstill_mode= x  : NORMAL, FREEWHEELING, BRAKING, STRONG_BRAKING");
    port.println("closed_loop_type=x  : OPEN_LOOP, MOVE_FROM_ENC, CLOSED_LOOP");
    port.println("mappingDirection=x  : reverse direction, 0 or 1");
    port.println("verboseOutput=x     : 0 or 1");
    port.println("values              : output current setup");
    port.println("led_flash           : flash LED1 twice");
    port.println("get_angle           : return current angle in degrees\n");
    return;
  }
  else if (cmd.equalsIgnoreCase("VALUES")) {
    port.println("\nCurrent Driver Setup:");
    port.print("steps_per_rev = "); port.println(stepsPerRev);
    port.print("enable = "); port.println(enabled1);
    port.print("microsteps = "); port.println(microsteps);
    port.print("voltage = "); port.println(setVoltage);
    port.print("current = "); port.println(current);
    port.print("speed = "); port.println(positionSpeed);
    port.print("standstill_mode = "); port.println(standstillMode);
    port.print("closed_loop_type = "); port.println(closedLoopType);
    port.print("mappingDirection = "); port.println(mappingDirection);
    port.print("verboseOutput = "); port.println(verboseOutput);
    port.println("");
    return;
  }
  else if (cmd.equalsIgnoreCase("led_flash")) {
    digitalWrite(LED1, HIGH); delay(300); digitalWrite(LED1, LOW);
    delay(200);
    digitalWrite(LED1, HIGH); delay(300); digitalWrite(LED1, LOW);
    return;
  }
  else if (cmd.equalsIgnoreCase("get_angle")) {
    port.println(angle);
    return;
  }
  else {
    // port.println("ERROR: Unknown command, enter 'help' for a list of commands");
    port.print("ERROR: Unknown command [");
    port.print(cmd); // This will show you exactly what hidden char is causing it
    port.println("], enter 'help' for a list of commands");
  }
}

unsigned long getStepDelay(float deg_per_sec, int steps_per_rev, int microsteps) {
  double total_steps_per_rev = steps_per_rev * microsteps;
  double steps_per_sec = (deg_per_sec / 360.0) * total_steps_per_rev;
  if (steps_per_sec <= 0) return 0;
  return (unsigned long)((1.0 / steps_per_sec) * 1e6);
}

void readEncoder(){
  int raw_counts;
  static int prev_raw_counts = 0;
  static signed long revolutions = 0;
  Wire.beginTransmission(AS5600_ADDRESS);
  Wire.write(0x0C); 
  Wire.endTransmission(false);
  Wire.requestFrom(AS5600_ADDRESS, 2);
  if (Wire.available() >= 2) {
    raw_counts = Wire.read() << 8 | Wire.read();
  }
  if (prev_raw_counts > 3000 && raw_counts < 1000) {
    revolutions++;
  } else if (prev_raw_counts < 1000 && raw_counts > 3000) {
    revolutions--;
  }
  prev_raw_counts = raw_counts;
  total_encoder_counts = raw_counts + (4096 * revolutions);
  angle = ((total_encoder_counts-encoder_offset) * 360.0) / 4096.0;
}

void configureSettings(){
  if (setVoltage == 5)       { digitalWrite(CFG1, HIGH); } 
  else if (setVoltage == 9)  { digitalWrite(CFG1, LOW); digitalWrite(CFG2, LOW); digitalWrite(CFG3, LOW); } 
  else if (setVoltage == 12) { digitalWrite(CFG1, LOW); digitalWrite(CFG2, LOW); digitalWrite(CFG3, HIGH); } 
  else if (setVoltage == 15) { digitalWrite(CFG1, LOW); digitalWrite(CFG2, HIGH); digitalWrite(CFG3, HIGH); } 
  else if (setVoltage == 20) { digitalWrite(CFG1, LOW); digitalWrite(CFG2, HIGH); digitalWrite(CFG3, LOW); }

  stepper_driver.setRunCurrent(current);
  stepper_driver.setMicrostepsPerStep(microsteps);
  stepper_driver.setStallGuardThreshold(stallThreshold);

  if (standstillMode == "NORMAL") stepper_driver.setStandstillMode(stepper_driver.NORMAL);
  else if (standstillMode == "FREEWHEELING") stepper_driver.setStandstillMode(stepper_driver.FREEWHEELING);
  else if (standstillMode == "BRAKING") stepper_driver.setStandstillMode(stepper_driver.BRAKING);
  else if (standstillMode == "STRONG_BRAKING") stepper_driver.setStandstillMode(stepper_driver.STRONG_BRAKING);
}

void readSettings(){ 
  preferences.begin("settings", false);
  enabled1 = preferences.getBool("enable", enabled1); 
  setVoltage = preferences.getInt("voltage", setVoltage); 
  microsteps = preferences.getInt("microsteps", microsteps); 
  current = preferences.getInt("current", current); 
  stallThreshold = preferences.getInt("stallThreshold", stallThreshold); 
  standstillMode = preferences.getString("standstillMode", standstillMode); 
  positionSpeed = preferences.getFloat("positionSpeed", positionSpeed); 
  stepsPerRev = preferences.getInt("stepsPerRev", stepsPerRev); 
  mappingDirection = preferences.getBool("mapDir", mappingDirection); 
  closedLoopType = preferences.getString("closedLoopType", closedLoopType); 
  verboseOutput = preferences.getBool("verboseOutput", verboseOutput); 
  preferences.end();
}

void writeSettings(){
  preferences.begin("settings", false);
  preferences.putBool("enable", enabled1); 
  preferences.putInt("voltage", setVoltage); 
  preferences.putInt("microsteps", microsteps); 
  preferences.putInt("current", current); 
  preferences.putInt("stallThreshold", stallThreshold); 
  preferences.putString("standstillMode", standstillMode); 
  preferences.putFloat("positionSpeed", positionSpeed); 
  preferences.putInt("stepsPerRev", stepsPerRev); 
  preferences.putBool("mapDir", mappingDirection); 
  preferences.putString("closedLoopType", closedLoopType); 
  preferences.putBool("verboseOutput", verboseOutput); 
  preferences.end();
  configureSettings();
}

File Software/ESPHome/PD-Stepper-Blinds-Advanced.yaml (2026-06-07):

# This example uses a custom TMC2209 component to control the PD Stepper
# It uses the encoder to get the current blind position so it will not lose home if blind is manually moved

# If the motor stalls it stops the motor and sets this as the new home/OPEN position (configurable)

# The "Home" button tries to move the blind up 120% of the set length and once a stall is detected it set this as the new home position (you may need to tune the stall theshold for you setup)
# This can be enabled at boot by setting home_on_boot to "true" in the substitutions block.


###################################
#########    SETTINGS   ###########
###################################
substitutions:
  #main settings you may want to change for your setup:
  device_name: "pd-stepper-blinds"     # ESPHome device name
  blinds_length: "30000"               # full blinds length (in encoder counts, 2048 per rev) !! CHANGE TO SUIT YOUR SETUP !! (make it negative to move in opposite direction!)
  encoder_invert: "true"               # set to "true" to invert the encoder direction mapping (may be different for some motors)
  stall_threshold: "20"                # higher = more sensitive, lower if stall triggering too often, 
  run_current: "800m"                  # motor current (800m = 800mA, 1 = 1A etc.) (current is set here, potentiometer is ignored)
  max_speed: "800"                     # steps/s
  acceleration: "1500"                 # steps/s²
  deceleration: "1500"                 # steps/s²
  pd_voltage: "15V"                    # PD voltage: 5V | 9V | 12V | 15V | 20V

  #additonal settings for different behaviours: (set all 3 to false to disable sensotless homing alltogether)
  home_on_boot: "false"                # set to "true" to automatically move and home the blind on boot
  stall_resets_home: "true"            # set to "false" to disable stall homing behaviour (motor will still stop on stall)
  stall_stops_motor: "true"            # set to "false" to disable motor stop on stall
  


external_components:
  - source: github://slimcdk/esphome-custom-components
    components: [tmc2209_hub, tmc2209, stepper]

globals:
  - id: encoder_tracking_
    type: int32_t[2]
    restore_value: no

  - id: encoder_offset_
    type: int32_t
    restore_value: no

  - id: sensored_home_pos
    type: int32_t
    restore_value: no
    initial_value: "0"

wifi:
  ssid: !secret wifi_ssid
  password: !secret wifi_password

api:

ota:
  - platform: esphome

logger:

esp32:
  board: esp32-s3-devkitc-1
  framework:
    type: esp-idf

esphome:
  name: ${device_name}
  platformio_options:
    board_build.flash_mode: dio
    upload_speed: 921600
  on_boot:
    - tmc2209.configure:
        microsteps: 4
        interpolation: true
        tcool_threshold: 400
    - tmc2209.stallguard:
        threshold: ${stall_threshold}
    - tmc2209.currents:
        ihold: 0
        tpowerdown: 0
        iholddelay: 0
        # irun: 16
        run_current: ${run_current}
        standstill_mode: freewheeling

    #set PD voltage: 5V=OFF/ON/OFF  9V=OFF/OFF/OFF  12V=OFF/OFF/ON  15V=OFF/ON/ON  20V=OFF/ON/OFF
    - if:
        condition:
          lambda: return std::string("${pd_voltage}") == "5V";
        then:
          - output.turn_off: { id: CFG1_pin }
          - output.turn_on:  { id: CFG2_pin }
          - output.turn_off: { id: CFG3_pin }
    - if:
        condition:
          lambda: return std::string("${pd_voltage}") == "9V";
        then:
          - output.turn_off: { id: CFG1_pin }
          - output.turn_off: { id: CFG2_pin }
          - output.turn_off: { id: CFG3_pin }
    - if:
        condition:
          lambda: return std::string("${pd_voltage}") == "12V";
        then:
          - output.turn_off: { id: CFG1_pin }
          - output.turn_off: { id: CFG2_pin }
          - output.turn_on:  { id: CFG3_pin }
    - if:
        condition:
          lambda: return std::string("${pd_voltage}") == "15V";
        then:
          - output.turn_off: { id: CFG1_pin }
          - output.turn_on:  { id: CFG2_pin }
          - output.turn_on:  { id: CFG3_pin }
    - if:
        condition:
          lambda: return std::string("${pd_voltage}") == "20V";
        then:
          - output.turn_off: { id: CFG1_pin }
          - output.turn_on:  { id: CFG2_pin }
          - output.turn_off: { id: CFG3_pin }

    - delay: 0.5s
    - lambda: id(sensored_home_pos) = id(encoder)->get_state();  # Set the home (open) position to power on position
    - if:
        condition:
          lambda: return ${home_on_boot};
        then:
          - button.press: home

i2c:
  sda: 8
  scl: 9
  scan: true

uart:
  tx_pin: 17
  rx_pin: 18
  baud_rate: 712000

output:
  - platform: ledc
    pin: 10
    id: led1_output

  - platform: ledc
    pin: 12
    id: led2_output

  - platform: gpio
    pin: GPIO38
    id: CFG1_pin
  - platform: gpio
    pin: GPIO48
    id: CFG2_pin
  - platform: gpio
    pin: GPIO47
    id: CFG3_pin
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

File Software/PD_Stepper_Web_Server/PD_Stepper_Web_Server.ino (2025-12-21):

/*
 * PD Stepper Webpage Example:
 * 
 *********  Software Version 1.0 ******************
 * 
 *    How to Use:
 * 1. Connect to created WiFi Network named "PD Stepper"
 * 2. On a browser visit 192.168.4.1
 * 
 *  For more info and to purchase PD Stepper kits visit:
 *  https://thingsbyjosh.com
 * 
 * TODO:
 * - More TMC error conditions (including power bad?)
 * - Stall guard disabled at lower speeds
 * - Fix non smooth position control (due to webserver interuptions)
*/



#include <WiFi.h>
#include <ESPAsyncWebServer.h> // https://github.com/ESP32Async/ESPAsyncWebServer (ENSURE THIS VERSION IS USED)
#include <AsyncTCP.h>  //https://github.com/ESP32Async/AsyncTCP/tree/main (ENSURE THIS VERSION IS USED)
#include <TMC2209.h> //  https://github.com/janelia-arduino/TMC2209/tree/main
#include <Preferences.h> //for saving to flash (instead of old EEPROM lib)
#include "index_html.h"

Preferences preferences;

//access point SSID and password (password = "" for no password)
const char *ssid = "PD Stepper";
const char *password = "";

AsyncWebServer server(80);

//TMC2209 setup
TMC2209 stepper_driver;
HardwareSerial & serial_stream = Serial2;
const long SERIAL_BAUD_RATE = 115200;

const uint8_t RUN_CURRENT_PERCENT = 100; //how much current to run at (0-100%)

//TMC2209 Stepper Driver
#define TMC_EN  21
#define STEP    5
#define DIR     6
#define MS1     1
#define MS2     2
#define SPREAD  7
#define TMC_TX  17
#define TMC_RX  18
#define DIAG    16
#define INDEX   11

//PD Trigger (CH224K)
#define PG      15  //power good singnal (dont enable stepper untill this is good)
#define CFG1    38
#define CFG2    48
#define CFG3    47

//Other
#define VBUS    4
#define NTC     7
#define LED1    10
#define LED2    12
#define SW1     35
#define SW2     36
#define SW3     37
#define AUX1    14
#define AUX2    13


//Global variables
int set_speed = 0;
bool PGState = 0; //state of the power good signal from PD sink IC
bool enabledState = 0;
bool state = 0; //step state

//AS5600 Hall Effect Encoder
#include <Wire.h> //For I2C for encoder
#define AS5600_ADDRESS 0x36 // I2C address of the AS5600 sensor
signed long total_encoder_counts = 0;
unsigned long lastEncRead = 0;

int mainFreq = 10; //Scheduled frequency = 100hz (for slower tasks, encoder reading etc)

//button read and debounce
bool incButtonState = HIGH;
bool decButtonState = HIGH;
bool resetButtonState = HIGH;
unsigned long lastDebounceTime = 0;
unsigned long debounceDelay = 50;

int buttonSpeed = 0;

//Voltage reading and calc
float VBusVoltage = 0;
float VREF = 3.3;
const float DIV_RATIO = 0.1189427313;  //20k&2.7K Voltage Divider

//Values received from websever save command
String enabled1 = "enabled";
String setVoltage = "12";
String microsteps = "32";
String current = "30";
String stallThreshold = "10";
String standstillMode = "NORMAL";

//variable updated in callback
volatile bool speedUpdatePending = false;
volatile int pendingSpeed = 0;
volatile bool posUpdatePending = false;
volatile int pendingPosMode = 0;

//Varaiables for position control (open loop)
signed long setPoint = 0;
signed long CurrentPosition = 0;
unsigned long lastStep = 0;

//read state of PG pin to display on webpage
String readPGState(){
  PGState = digitalRead(PG);
  if (PGState == 0){
    return ("Power Good");
  } else {
    return ("Power Bad");
  }
}

// read VBUS voltage to display on webpage
String readVoltage() {
  uint32_t mvSum = 0;
  int samples = 10; // Average 10 readings to smooth out electrical noise

  for (int i = 0; i < samples; i++) {
    mvSum += analogReadMilliVolts(VBUS);
  }

  float avgMilliVolts = (float)mvSum / (float)samples;
  
  // avgMilliVolts / 1000.0 = Actual voltage at the ESP32 pin
  // Dividing by DIV_RATIO scales it back up to the battery/VBUS voltage
  VBusVoltage = (avgMilliVolts / 1000.0) / DIV_RATIO;

  // Returning with 2 decimal places for better readability
  return String(VBusVoltage, 2) + "V";
}

//read encoder pos to display on webpage
String readEncoderPos(){
  readEncoder();
  return String(total_encoder_counts);
}

String readTMCStatus(){
  bool hardware_disabled = stepper_driver.hardwareDisabled();
  if (hardware_disabled){
   return ("Hardware Disabled");
  }

  TMC2209::Status status = stepper_driver.getStatus();
  if (status.over_temperature_warning){
    return ("Over Temp Warning");
  }
  else if (status.over_temperature_shutdown){
    return ("Over Temp Shutdown");
  }
  return ("No Errors");
}

String readStallStatus(){
  return String(stepper_driver.getStallGuardResult());
//  if (digitalRead(DIAG) == HIGH){
//    return ("Stalled");
//  } else{
//    return ("Not Stalled");
//  }
}


//updates placeholder varibles in the HTML code //puts current arduino settings into webpage
//Puts stored values into the HTML value
String processor(const String& var)
{
  if(var == "enabled1"){
    if (enabled1 == "enabled"){
      return "checked";
    } else { return "";}
  }

  if (var == "microsteps"){
    return String(microsteps);
  }

  if(var == "voltage"){
     return String(setVoltage);
  }

  if(var == "current"){
     return String(current);
  }

  if(var == "stall_threshold"){
     return String(stallThreshold);
  }

  if(var == "standstill_mode"){
     return String(standstillMode);
  }
}
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

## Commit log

2024-07-01 ESPHome example updated to include LED control and read VBUS voltage
2024-08-24 Updated heat spreader/spacer thickness
    [Heat Spreader (2.5mm).step]
2024-08-28 Added 3D model of PCB
2024-08-29 Heat spreader update
    [Heat Spreader (2.5mm).step]
2024-10-11 PCB Source Files Added
    [PD Stepper V1.SchDoc]
2024-11-05 Update Assembly instructions
2024-11-20 Update PD_Stepper_Web_Server.ino
    Fixed incorrect IP address
    [PD_Stepper_Web_Server.ino]
2025-01-15 Added current value input
2025-01-15 Update getting started with current set info
2025-02-01 Import tmc2209_hub in PD-Stepper-Blinds-Advanced.yaml
2025-02-01 Import tmc2209_hub in PD-Stepper-Position-Control.yaml
2025-02-11 Update PD-Stepper-Blinds-Advanced.yaml
    suppress aggressive encoder polling
2025-02-11 Update PD-Stepper-Position-Control.yaml
    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
2025-02-18 Add option to reverse encoder input for motors wired with different pinout
    [PD-Stepper-Blinds-Advanced.yaml]
2025-12-04 Update README.md to include cable type Note
2025-12-09 Update README.md
    Added Note about magnet height
2025-12-21 Example improvements. Webserver Libraries changed, VBUS reading uses factory calibration.
2026-01-17 Update README.md with suggested motor model
2026-01-17 Update example with stall detection enabled and better homing logic
    [PD-Stepper-Blinds-Advanced.yaml]
2026-06-06 Updated to make it easier to configure and fixed bug in inverted encoder setting
    [PD-Stepper-Blinds-Advanced.yaml]
